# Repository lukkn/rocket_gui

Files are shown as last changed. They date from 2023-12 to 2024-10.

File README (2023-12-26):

# Communication between Teensy and MOTE board

## SETUP INSTRUNCTIONS
1. Connect each MoTE board used to 12V power, connecting to the 2 pins on J1 closest to the top of the board. Upper pin is power, lower pin is ground. Connect each teensy to the router via ethernet, and connect the control console to the same router
2. In the file "Example SD card Root/sensor_min_test.csv", add all necessary sensors and/or actuators, make sure to specify mote number, pin number, and sensor type (see below for sensor types). For ADCs, the pin number is weird. The first digit is the ADC number (counting from the left, starting at 0), and the second digit is the pin number. E.g. ADC pin number 11 is J20, pin 1. For 2ch ADCs, use a pin number of 0 for the left two pins and pin number 1 for the right two pins.
3. Once the teensy is powered and conneted, run gui.py, the orange status light on the teensy will be on if there is a connection. If you need to change any config informaiton, REBOOT THE TEENSY!!

## Sensor Types
* Teensy ADC
* i2c ADC 1ch
* i2c ADC 2ch
* servoPWM
* servoPWM_12V
* Binary GPIO

## Identifying each Teensy and MOTE Board

Each MOTE board will hold a teensy. We can identify each by their unique MOTE number.

They will be last digit of each MOTE's static IP. That digit will be saved as an ascii-value in MoteNumber.txt in SD card.

## Communication Protocol

Protocol used between Teensy and the GUI will be done in **UDP**.

## Types of Functions

There are 4 types of read functions for sensors and 2 types of write functions for actuators.

Each function is assigned an Interface Type Number.

**Read functions:**

1. Teensy ADC
2. i2c ADC 1 channel (ads122c4)
3. i2c ADC 2 channel (ads122c4) (for thermocouple)
4. flowmeter counter

**Write functions:**

5. servo PWM
6. binary gpio

| Operation | Interface Type Number | Sensor/Actuator |
| --- | --- | --- |
| READ | 1 | Teensy ADC |
| READ | 2 | I2C ADC 1 channel (ads122c4) |
| READ | 3 | I2C ADC 2 channel (ads122c4) (for thermocouple) |
| READ | 4 | Flowmeter Counter |
| WRITE | 5 | Servo PWM |
| WRITE | 6 | Binary GPIO |

## Packet Data Structure

Each packet will be sent and received as a **byte array**.

### Sensor Config Commands (Server -> Teensy):

**Byte Array**

| Byte 1  | Byte 2 |
| --- | --- |
| pin_num | config_byte |

**Bit Array of `config_byte`**

| Bit 1 (MSB) | Bit 2 | Bit 3 - 8 |
| --- | --- | --- |
| actuator write command = 0 (since this is not an actuator write command) | actuator state (not used in sensor config packets) | Interface Type Number |

**NB 1.** Byte variable can be of type `char` or `uint8` or `hex` as its eight bits long.

**NB 2.** Given we are dealing with sensors, _Interface Type Number_ is either 1, 2, or 3, and _Bit 1_ and _Bit 2_ are 0.

**NB 3.** Knowing the pin number and sensor type is enough info to call the correct sensor read function, which takes pin number as argument.

### Actuator Write Commands (Server -> Teensy):

**Byte Array**

| Byte 1  | Byte 2 |
| --- | --- |
| pin_num | config_byte |

**Bit Array of `config_byte`**

| Bit 1 (MSB) | Bit 2 | Bit 3 - 8 |
| --- | --- | --- |
| Actuator write command = 1 (because this is an actuator write command) | actuator state | Interface Type Number |

**NB 4.** Given we are dealing with actuators, _Interface Type Number_ is either 4 or 5.

### Sensor Data (Teensy -> Server)

The byte array ar however many sensors there are in each teensy, whose information is provided in config file

Each Teensy will send to the server a differently lengthed byte array.

**Byte Array**

| Byte 1 | Byte 2-5 | Byte 6 | Byte 7-10 | etc. (5 bytes per sensor: 1 pin byte, 4 data bytes) |
| --- | --- | --- | --- | --- |
| pin_num of sensor_1 | data_value of sensor_1 | pin_num of sensor_2 | data_value of sensor_2 | Pin & dava_val of sensors_3-to-n |

**NB 5.** _data_value_ for each sensor is an int (4 bytes).

# To compile Teensy code from command line (without Arduino IDE). NOT USED FOR CURRENT CODE

If cloning this repo to compile firmware, you need to run the following once (to download the teensy4 core):

```
git submodule init
git submodule update
```

To update submodules:

```
git submodule foreach git pull

dependencies:
arm-none-eabi-newlib
arm-none-eabi-gcc
```

The PWMServo library is modified to INVERT the PWM duty cycle because we're using a MOSFET to drive a higher voltage, which inverts the signal
line 198 of PMWServo.cpp

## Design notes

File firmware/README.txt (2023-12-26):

Instructions to build code:

STEP 1
* Open the folder platformio_build in the arduino IDE
* MAKE SURE Teensyduino IS INSTALLED!!!

STEP 2
* Make sure the board selected in the arduino IDE is Teensy 4.1
* If it gives you an error about "sensors_and_servos.h" not found, copy the folder lib/sensors_and_servos into your arduino libraries folder, or make a symlink
	> A symlink is probably better, because if you copy the code into the arudino library and then edit it there, it won't make it into any git commits unless you specifically copy it back
* If you're on Windows, it should be the arudino libraries folder in "Program Files (x86)/Arduino/Libraries"
* If it complains about any other libraries not being installed, install them using the arduino library manager

STEP 3
* Connect the mote board to your computer with an appropriate cable
* Press the "deploy" button in the arduino IDE
* When prompted by Teensyduino, press the button on the mote board
* It should say "done deploying" or something like that
* SEE NEXT STEP **BEFORE** USING MOTE OR POWERING IT WITH A DC POWER SUPPLY

STEP 4
* Make sure the MOTE board is powered either via USB or by a DC Power Supply, NOT BOTH
* If powered via usb, take care to make sure it is only via some kind of hub. Plugging it directly into a computer might damage said computer, do so only at own risk.
* Connect MOTE to a control computer via ethernet, and via USB if you need to read serial outputs (see above note about not combining DC/USB power and about PC saftey with usb)
* Disconnect from BU wifi when communicating with mote via ethernet
* Run the GUI in the Client_GUI folder (see the README file there)
* Make sure the GUI is reading the correct config csv file, and that it is configured correctly.

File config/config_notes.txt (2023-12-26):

Spreadsheet with all components found here:
https://docs.google.com/spreadsheets/d/1thmBCXt51pdb-lDczYVI7NMO4nz0p3LYw5bA1uRQ-AM/edit?usp=sharing

Pin numbers are not shown on this spreadsheet, a pin number of -1 in a config file means the number is unknown.

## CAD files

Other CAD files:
FlaskGUI/python_flask_and_flaskio_and_eventlet_libraries/greenlet/platform/switch_x64_masm.obj
FlaskGUI/python_flask_and_flaskio_and_eventlet_libraries/greenlet/platform/switch_arm64_masm.obj

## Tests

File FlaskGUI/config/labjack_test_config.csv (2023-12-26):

Mote id | Sensor or Actuator | Interface Type | Human Name | Pin | P and ID | unit | min | max
10 | sensor | i2c ADC 2ch | AIN0 | AIN1-AIN0 | AIN0 | Volts | 0 | 5

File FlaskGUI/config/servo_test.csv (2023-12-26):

Mote id | Sensor or Actuator | Interface Type | Human Name | Pin | P and ID
1 | sensor | i2c ADC 1ch | Analog_1 | 42
1 | actuator | servoPWM | Servo_1_5V | 9
1 | actuator | servoPWM | Servo_2_5V | 8
1 | actuator | servoPWM | Servo_3_5V | 7
1 | actuator | servoPWM | Servo_1_7V | 29
1 | actuator | servoPWM | Servo_2_7V | 27
1 | actuator | servoPWM | Servo_3_7V | 25

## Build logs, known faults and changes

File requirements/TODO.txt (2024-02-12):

Functional:
- CRITICAL: ACK/NACK indicator on actuators. Keep current "last sent command" indicator
- Make the ABORT button work. There should be a way to load an abort script from the GUI, 
    and a warning if you try to run a sequence with no abort script loaded
- Forbid arming without a loaded config, and forbid sequences from running disarmed
- Get rid of all the submit buttons, "upload" should inherently submit
- There should be connected indicators
- If a box has sent a packet in the last 1.5s, assume it's there. Otherwise, assume it's disconnected
- Buttons should be greyed out / unclickable when system is disarmed OR disconnected
- Verify autoseq with actuators before autoseq runs
- Arm/Disarm button spamming while app.py is not running will lead to all commands being received on restart ;; check this for actuator presses as well, we default to disarm so fixing the first issue should fix the second but not a good aproach

Stylistic:
- Make it look nice!
- Make the sensor graphs a 2xN grid

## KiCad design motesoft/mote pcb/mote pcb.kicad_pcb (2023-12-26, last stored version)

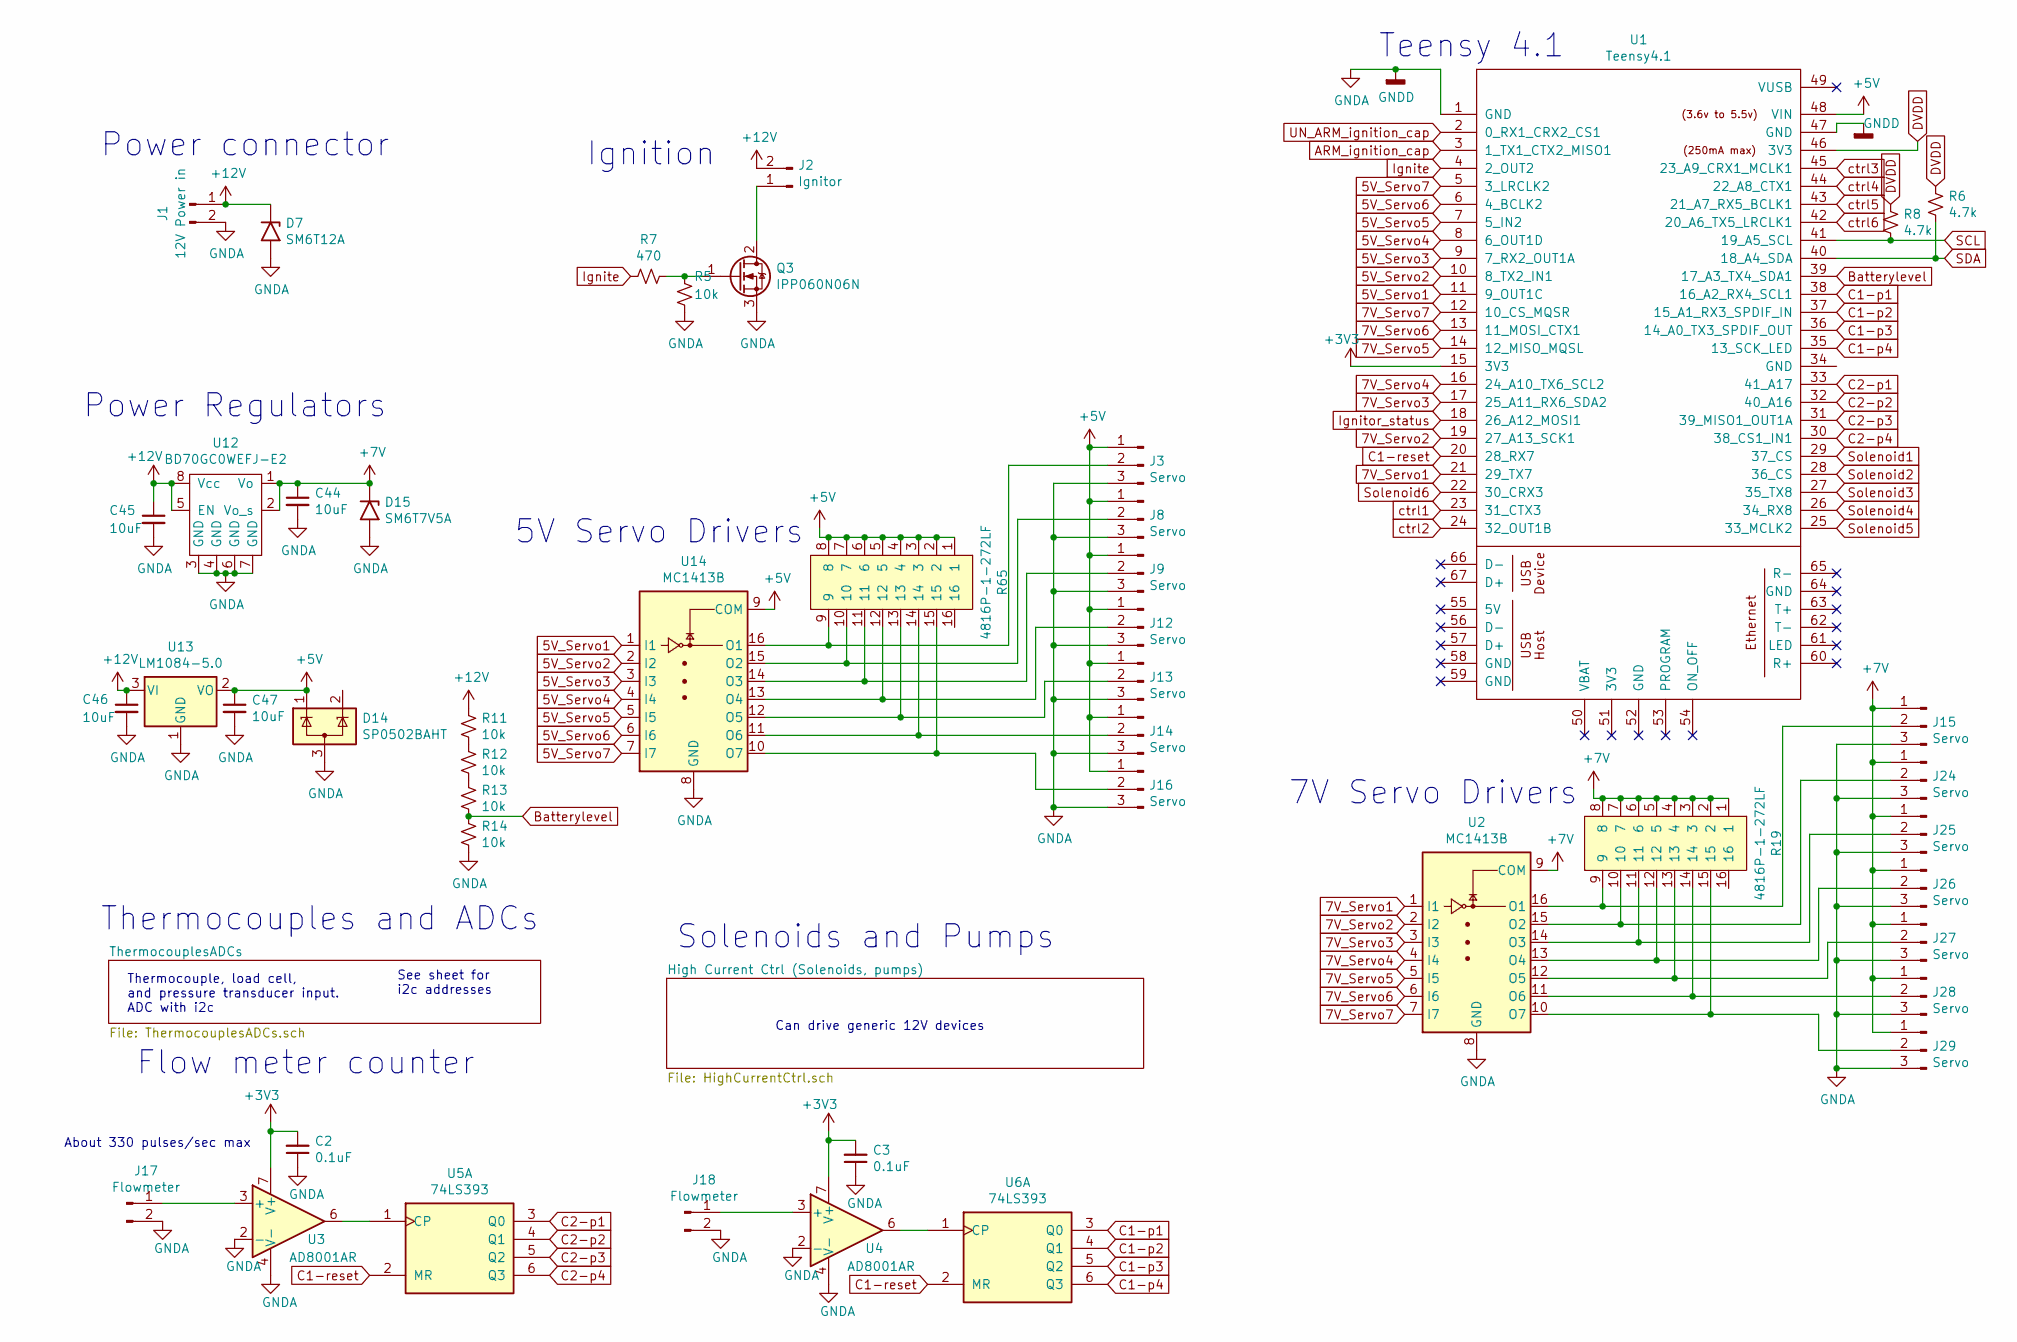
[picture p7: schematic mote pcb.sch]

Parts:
C2, C3: 0.1uF; C_0603_1608Metric_Pad1.08x0.95mm_HandSolder; LCSC Part # C14663
C44, C45, C46, C47: 10uF; C_0603_1608Metric_Pad1.08x0.95mm_HandSolder; LCSC Part # C19702
D7: SM6T12A; D_SMB
D14: SP0502BAHT; SOT-23
D15: SM6T7V5A; D_SMB
J1: 12V Power in; JST_EH_B4B-EH-A_1x04_P2.50mm_Vertical
J2: Ignitor; JST_EH_B4B-EH-A_1x04_P2.50mm_Vertical
J3, J8, J9, J12, J13, J14, J15, J16, J24, J25, J26, J27, J28, J29: Servo; JST_EH_B4B-EH-A_1x04_P2.50mm_Vertical
J17, J18: Flowmeter; JST_EH_B4B-EH-A_1x04_P2.50mm_Vertical
Q3: IPP060N06N; TO-220-3_Vertical
R5, R11, R12, R13, R14: 10k; R_0603_1608Metric_Pad0.98x0.95mm_HandSolder; LCSC Part # C25804
R6, R8: 4.7k; R_0603_1608Metric_Pad0.98x0.95mm_HandSolder; LCSC Part # C23162
R7: 470; R_0603_1608Metric_Pad0.98x0.95mm_HandSolder; LCSC Part # C23179
R19, R65: 4816P-1-272LF; SOIC-16W_5.3x10.2mm_P1.27mm
U1: Teensy4.1; Teensy41
U2, U14: MC1413B; SOIC-16_3.9x9.9mm_P1.27mm
U3, U4: AD8001AR; SOIC-8_3.9x4.9mm_P1.27mm
U5, U6: 74LS393; SOIC-14_3.9x8.7mm_P1.27mm
U12: BD70GC0WEFJ-E2; SOIC-8-1EP_3.9x4.9mm_P1.27mm_EP2.29x3mm_ThermalVias
U13: LM1084-5.0; TO-263-3_TabPin2

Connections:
5V_Servo1: U1.11 (9_OUT1C), U14.1 (I1)
5V_Servo2: U1.10 (8_TX2_IN1), U14.2 (I2)
5V_Servo3: U1.9 (7_RX2_OUT1A), U14.3 (I3)
5V_Servo4: U1.8 (6_OUT1D), U14.4 (I4)
5V_Servo5: U1.7 (5_IN2), U14.5 (I5)
5V_Servo6: U1.6 (4_BCLK2), U14.6 (I6)
5V_Servo7: U1.5 (3_LRCLK2), U14.7 (I7)
7V_Servo1: U1.21 (29_TX7), U2.1 (I1)
7V_Servo2: U1.19 (27_A13_SCK1), U2.2 (I2)
7V_Servo3: U1.17 (25_A11_RX6_SDA2), U2.3 (I3)
7V_Servo4: U1.16 (24_A10_TX6_SCL2), U2.4 (I4)
7V_Servo5: U1.14 (12_MISO_MQSL), U2.5 (I5)
7V_Servo6: U1.13 (11_MOSI_CTX1), U2.6 (I6)
7V_Servo7: U1.12 (10_CS_MQSR), U2.7 (I7)
+3V3: C2.2, C3.2, U1.15 (3V3), U3.7 (V+), U4.7 (V+); also elsewhere on the board
+5V: C47.1, D14.1 (K), J3.1, J8.1, J9.1, J12.1, J13.1, J14.1, J16.1, R65.1, R65.2, R65.3, R65.4, R65.5, R65.6, R65.7, R65.8, U1.48 (VIN), U13.2 (VO), U14.9 (COM)
+7.5V: C44.1, D15.1 (A1), J15.1, J24.1, J25.1, J26.1, J27.1, J28.1, J29.1, R19.1, R19.2, R19.3, R19.4, R19.5, R19.6, R19.7, R19.8, U2.9 (COM), U12.1 (Vo), U12.2 (Vo_s)
+12V: C45.1, C46.1, D7.1 (A1), J1.1, J2.2, R11.1, U12.5 (EN), U12.8 (Vcc), U13.3 (VI); also elsewhere on the board
Batterylevel: R13.2, R14.1, U1.39 (17_A3_TX4_SDA1)
C1-p1: U1.38 (16_A2_RX4_SCL1), U6.3 (Q0)
C1-p2: U1.37 (15_A1_RX3_SPDIF_IN), U6.4 (Q1)
C1-p3: U1.36 (14_A0_TX3_SPDIF_OUT), U6.5 (Q2)
C1-p4: U1.35 (13_SCK_LED), U6.6 (Q3)
C1-reset: U1.20 (28_RX7), U5.2 (MR), U6.2 (MR)
C2-p1: U1.33 (41_A17), U5.3 (Q0)
C2-p2: U1.32 (40_A16), U5.4 (Q1)
C2-p3: U1.31 (39_MISO1_OUT1A), U5.5 (Q2)
C2-p4: U1.30 (38_CS1_IN1), U5.6 (Q3)
DVDD: R6.1, R8.1, U1.46 (3V3)
GNDA: C2.1, C3.1, C44.2, C45.2, C46.2, C47.2, D7.2 (A2), D14.3 (A), D15.2 (A2), J1.2, J3.3, J8.3, J9.3, J12.3, J13.3, J14.3, J15.3, J16.3, J17.2, J18.2, J24.3, J25.3, J26.3, J27.3, J28.3, J29.3, Q3.3 (S), R5.2, R14.2, U1.1 (GND), U1.47 (GND), U2.8 (GND), U3.2 (-), U3.4 (V-), U4.2 (-), U4.4 (V-), U12.3 (GND), U12.4 (GND), U12.6 (GND), U12.7 (GND), U13.1 (GND), U14.8 (GND); also elsewhere on the board
Ignite: R7.2, U1.4 (2_OUT2)
unnamed: J2.1, Q3.2 (D)
unnamed: J3.2, R65.9, U14.16 (O1)
unnamed: J8.2, R65.10, U14.15 (O2)
unnamed: J9.2, R65.11, U14.14 (O3)
unnamed: J12.2, R65.12, U14.13 (O4)
unnamed: J13.2, R65.13, U14.12 (O5)
unnamed: J14.2, R65.14, U14.11 (O6)
unnamed: J15.2, R19.9, U2.16 (O1)
unnamed: J16.2, R65.15, U14.10 (O7)
unnamed: J17.1, U3.3 (+)
unnamed: J18.1, U4.3 (+)
unnamed: J24.2, R19.10, U2.15 (O2)
unnamed: J25.2, R19.11, U2.14 (O3)
unnamed: J26.2, R19.12, U2.13 (O4)
unnamed: J27.2, R19.13, U2.12 (O5)
unnamed: J28.2, R19.14, U2.11 (O6)
unnamed: J29.2, R19.15, U2.10 (O7)
unnamed: Q3.1 (G), R5.1, R7.1
unnamed: R11.2, R12.1
unnamed: R12.2, R13.1
unnamed: U3.6, U5.1 (CP)
unnamed: U4.6, U6.1 (CP)
SCL: R8.2, U1.41 (19_A5_SCL); also elsewhere on the board
SDA: R6.2, U1.40 (18_A4_SDA); also elsewhere on the board
Solenoid1: U1.29 (37_CS); also elsewhere on the board
Solenoid2: U1.28 (36_CS); also elsewhere on the board
Solenoid3: U1.27 (35_TX8); also elsewhere on the board
Solenoid4: U1.26 (34_RX8); also elsewhere on the board
Solenoid5: U1.25 (33_MCLK2); also elsewhere on the board
Solenoid6: U1.22 (30_CRX3); also elsewhere on the board
ctrl1: U1.23 (31_CTX3); also elsewhere on the board
ctrl2: U1.24 (32_OUT1B); also elsewhere on the board
ctrl3: U1.45 (23_A9_CRX1_MCLK1); also elsewhere on the board
ctrl4: U1.44 (22_A8_CTX1); also elsewhere on the board
ctrl5: U1.43 (21_A7_RX5_BCLK1); also elsewhere on the board
ctrl6: U1.42 (20_A6_TX5_LRCLK1); also elsewhere on the board

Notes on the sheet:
Thermocouple, load cell, and pressure transducer input. ADC with i2c
See sheet for i2c addresses
Ignition
Thermocouples and ADCs
Flow meter counter
Teensy 4.1
About 330 pulses/sec max
Power connector
7V Servo Drivers
Can drive generic 12V devices
Solenoids and Pumps
5V Servo Drivers
Power Regulators

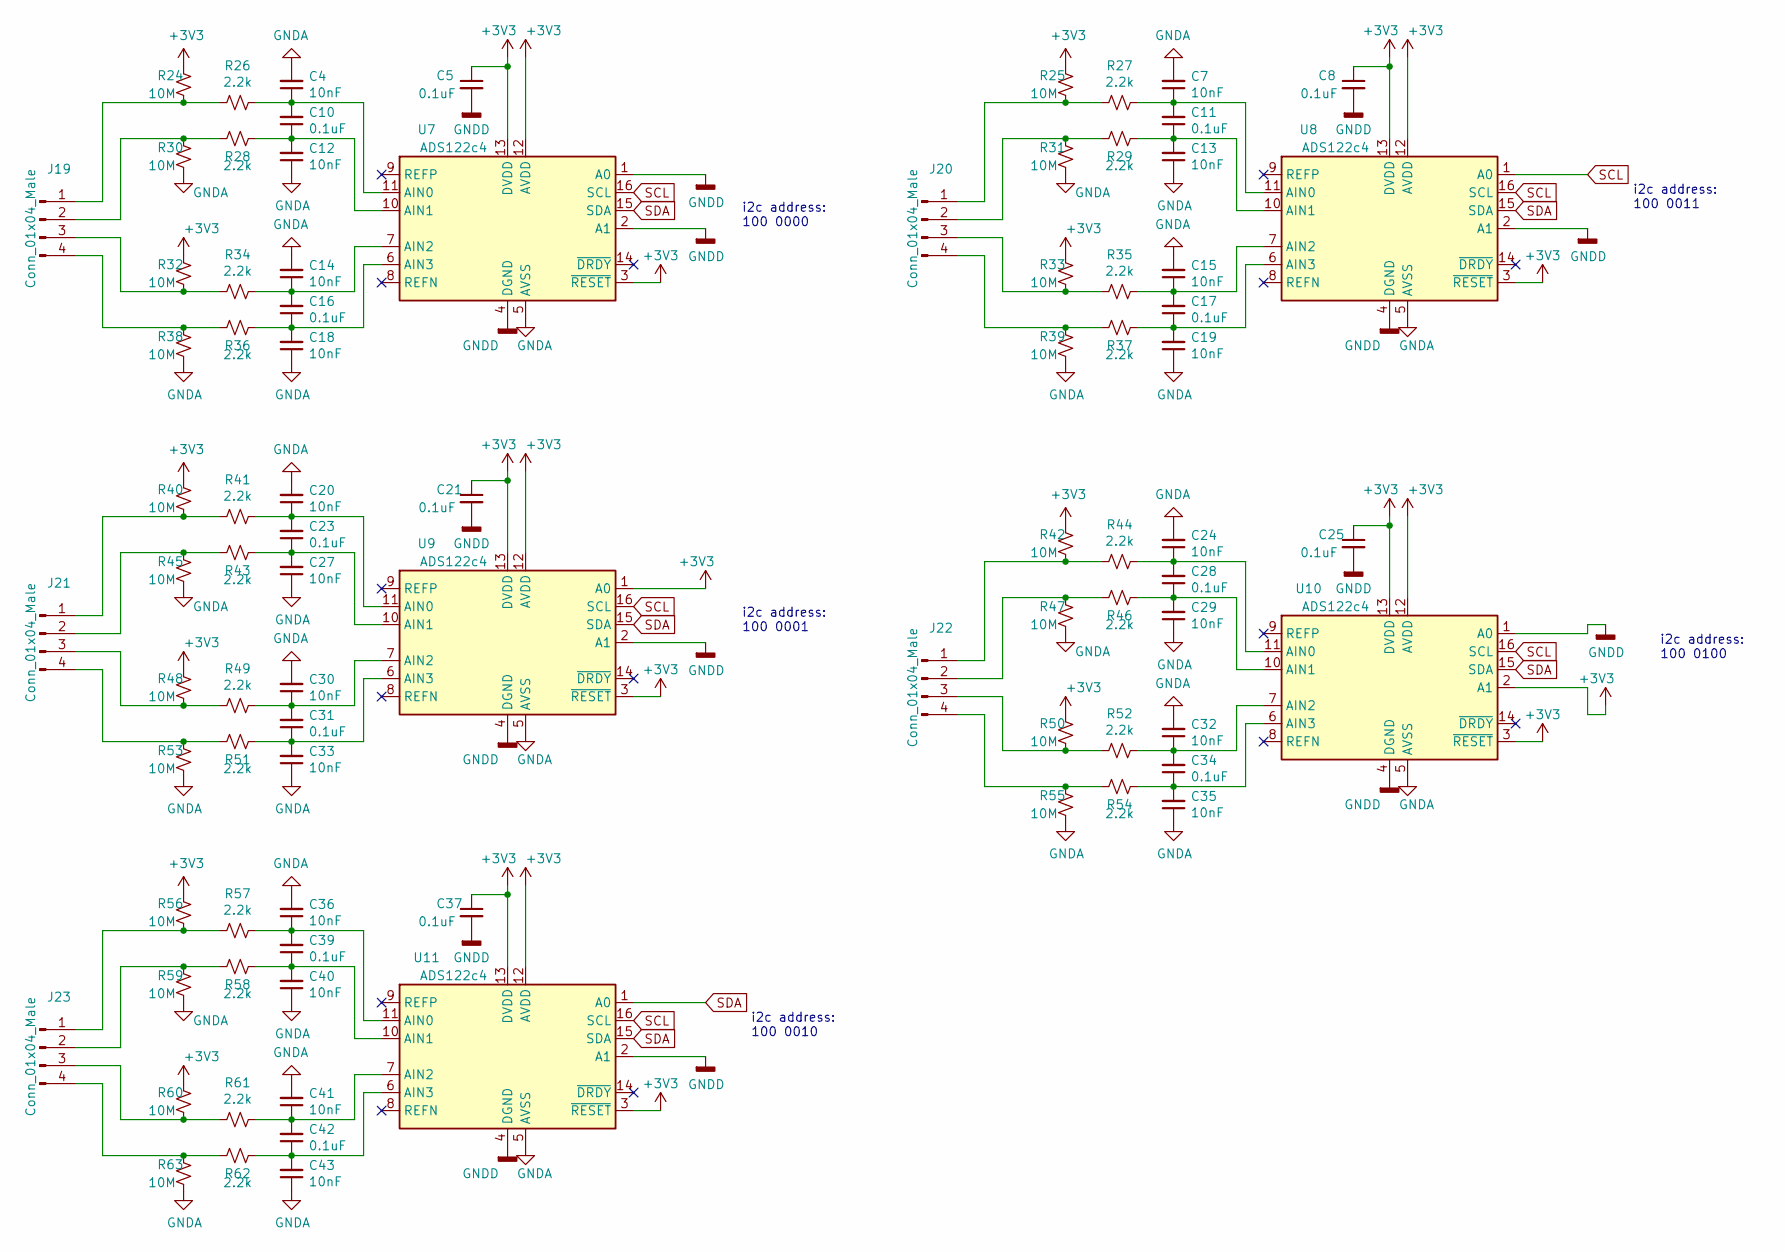
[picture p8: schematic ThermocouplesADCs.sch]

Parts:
C4, C7, C12, C13, C14, C15, C18, C19, C20, C24, C27, C29, C30, C32, C33, C35, C36, C40, C41, C43: 10nF; C_0603_1608Metric_Pad1.08x0.95mm_HandSolder; LCSC Part # C57112
C5, C8, C10, C11, C16, C17, C21, C23, C25, C28, C31, C34, C37, C39, C42: 0.1uF; C_0603_1608Metric_Pad1.08x0.95mm_HandSolder; LCSC Part # C14663
J19, J20, J21, J22, J23: Conn_01x04_Male; JST_EH_B4B-EH-A_1x04_P2.50mm_Vertical
R24, R25, R30, R31, R32, R33, R38, R39, R40, R42, R45, R47, R48, R50, R53, R55, R56, R59, R60, R63: 10M; R_0603_1608Metric_Pad0.98x0.95mm_HandSolder; LCSC Part # C7250
R26, R27, R28, R29, R34, R35, R36, R37, R41, R43, R44, R46, R49, R51, R52, R54, R57, R58, R61, R62: 2.2k; R_0603_1608Metric_Pad0.98x0.95mm_HandSolder; LCSC Part # C4190
U7, U8, U9, U10, U11: ADS122c4; TSSOP-16_4.4x5mm_P0.65mm

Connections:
+3V3: C5.1, C8.1, C21.1, C25.1, C37.1, R24.2, R25.2, R32.2, R33.2, R40.2, R42.2, R48.2, R50.2, R56.2, R60.2, U7.3 (~RESET), U7.12 (AVDD), U7.13 (DVDD), U8.3 (~RESET), U8.12 (AVDD), U8.13 (DVDD), U9.1 (A0), U9.3 (~RESET), U9.12 (AVDD), U9.13 (DVDD), U10.2 (A1), U10.3 (~RESET), U10.12 (AVDD), U10.13 (DVDD), U11.3 (~RESET), U11.12 (AVDD), U11.13 (DVDD); also elsewhere on the board
GNDA: C4.2, C5.2, C7.2, C8.2, C12.1, C13.1, C14.2, C15.2, C18.1, C19.1, C20.2, C21.2, C24.2, C25.2, C27.1, C29.1, C30.2, C32.2, C33.1, C35.1, C36.2, C37.2, C40.1, C41.2, C43.1, R30.1, R31.1, R38.1, R39.1, R45.1, R47.1, R53.1, R55.1, R59.1, R63.1, U7.1 (A0), U7.2 (A1), U7.4 (DGND), U7.5 (AVSS), U8.2 (A1), U8.4 (DGND), U8.5 (AVSS), U9.2 (A1), U9.4 (DGND), U9.5 (AVSS), U10.1 (A0), U10.4 (DGND), U10.5 (AVSS), U11.2 (A1), U11.4 (DGND), U11.5 (AVSS); also elsewhere on the board
unnamed: C10.1, C12.2, R28.2, U7.10 (AIN1)
unnamed: C4.1, C10.2, R26.2, U7.11 (AIN0)
unnamed: C11.1, C13.2, R29.2, U8.10 (AIN1)
unnamed: C7.1, C11.2, R27.2, U8.11 (AIN0)
unnamed: C14.1, C16.2, R34.2, U7.7 (AIN2)
unnamed: C15.1, C17.2, R35.2, U8.7 (AIN2)
unnamed: C16.1, C18.2, R36.2, U7.6 (AIN3)
unnamed: C17.1, C19.2, R37.2, U8.6 (AIN3)
unnamed: C20.1, C23.2, R41.2, U9.11 (AIN0)
unnamed: C23.1, C27.2, R43.2, U9.10 (AIN1)
unnamed: C24.1, C28.2, R44.2, U10.11 (AIN0)
unnamed: C28.1, C29.2, R46.2, U10.10 (AIN1)
unnamed: C30.1, C31.2, R49.2, U9.7 (AIN2)
unnamed: C31.1, C33.2, R51.2, U9.6 (AIN3)
unnamed: C32.1, C34.2, R52.2, U10.7 (AIN2)
unnamed: C34.1, C35.2, R54.2, U10.6 (AIN3)
unnamed: C36.1, C39.2, R57.2, U11.11 (AIN0)
unnamed: C39.1, C40.2, R58.2, U11.10 (AIN1)
unnamed: C41.1, C42.2, R61.2, U11.7 (AIN2)
unnamed: C42.1, C43.2, R62.2, U11.6 (AIN3)
unnamed: J19.1, R24.1, R26.1
unnamed: J19.2, R28.1, R30.2
unnamed: J19.3, R32.1, R34.1
unnamed: J19.4, R36.1, R38.2
unnamed: J20.1, R25.1, R27.1
unnamed: J20.2, R29.1, R31.2
unnamed: J20.3, R33.1, R35.1
unnamed: J20.4, R37.1, R39.2
unnamed: J21.1, R40.1, R41.1
unnamed: J21.2, R43.1, R45.2
unnamed: J21.3, R48.1, R49.1
unnamed: J21.4, R51.1, R53.2
unnamed: J22.1, R42.1, R44.1
unnamed: J22.2, R46.1, R47.2
unnamed: J22.3, R50.1, R52.1
unnamed: J22.4, R54.1, R55.2
unnamed: J23.1, R56.1, R57.1
unnamed: J23.2, R58.1, R59.2
unnamed: J23.3, R60.1, R61.1
unnamed: J23.4, R62.1, R63.2
SCL: U7.16 (SCL), U8.1 (A0), U8.16 (SCL), U9.16 (SCL), U10.16 (SCL), U11.16 (SCL); also elsewhere on the board
SDA: U7.15 (SDA), U8.15 (SDA), U9.15 (SDA), U10.15 (SDA), U11.1 (A0), U11.15 (SDA); also elsewhere on the board

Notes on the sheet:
i2c address: 100 0000
i2c address: 100 0001
i2c address: 100 0010
i2c address: 100 0011
i2c address: 100 0100

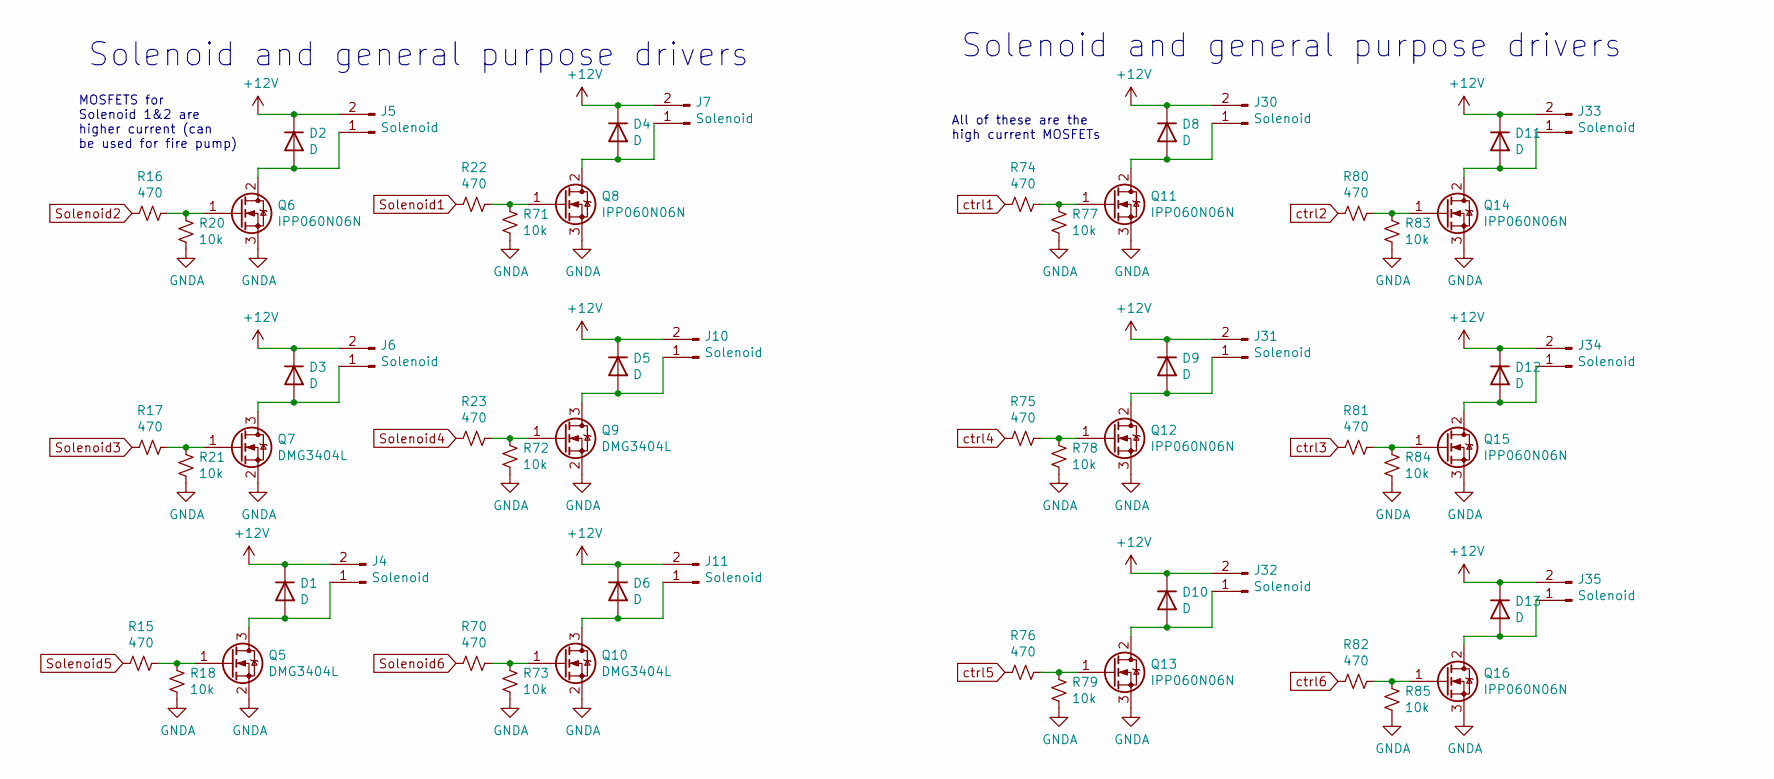
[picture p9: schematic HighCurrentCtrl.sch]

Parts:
D1, D2, D3, D4, D5, D6, D8, D9, D10, D11, D12, D13: D; D_SOD-123; LCSC Part # C8598
J4, J5, J6, J7, J10, J11, J30, J31, J32, J33, J34, J35: Solenoid; JST_EH_B4B-EH-A_1x04_P2.50mm_Vertical
Q5, Q7, Q9, Q10: DMG3404L; SOT-23
Q6, Q8, Q11, Q12, Q13, Q14, Q15, Q16: IPP060N06N; TO-220-3_Vertical
R15, R16, R17, R22, R23, R70, R74, R75, R76, R80, R81, R82: 470; R_0603_1608Metric_Pad0.98x0.95mm_HandSolder; LCSC Part # C23179
R18, R20, R21, R71, R72, R73, R77, R78, R79, R83, R84, R85: 10k; R_0603_1608Metric_Pad0.98x0.95mm_HandSolder; LCSC Part # C25804

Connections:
+12V: D1.1 (K), D2.1 (K), D3.1 (K), D4.1 (K), D5.1 (K), D6.1 (K), D8.1 (K), D9.1 (K), D10.1 (K), D11.1 (K), D12.1 (K), D13.1 (K), J4.2, J5.2, J6.2, J7.2, J10.2, J11.2, J30.2, J31.2, J32.2, J33.2, J34.2, J35.2; also elsewhere on the board
GNDA: Q5.2 (S), Q6.3 (S), Q7.2 (S), Q8.3 (S), Q9.2 (S), Q10.2 (S), Q11.3 (S), Q12.3 (S), Q13.3 (S), Q14.3 (S), Q15.3 (S), Q16.3 (S), R18.2, R20.2, R21.2, R71.2, R72.2, R73.2, R77.2, R78.2, R79.2, R83.2, R84.2, R85.2; also elsewhere on the board
unnamed: D1.2 (A), J4.1, Q5.3 (D)
unnamed: D2.2 (A), J5.1, Q6.2 (D)
unnamed: D3.2 (A), J6.1, Q7.3 (D)
unnamed: D4.2 (A), J7.1, Q8.2 (D)
unnamed: D5.2 (A), J10.1, Q9.3 (D)
unnamed: D6.2 (A), J11.1, Q10.3 (D)
unnamed: D8.2 (A), J30.1, Q11.2 (D)
unnamed: D9.2 (A), J31.1, Q12.2 (D)
unnamed: D10.2 (A), J32.1, Q13.2 (D)
unnamed: D11.2 (A), J33.1, Q14.2 (D)
unnamed: D12.2 (A), J34.1, Q15.2 (D)
unnamed: D13.2 (A), J35.1, Q16.2 (D)
unnamed: Q5.1 (G), R15.1, R18.1
unnamed: Q6.1 (G), R16.1, R20.1
unnamed: Q7.1 (G), R17.1, R21.1
unnamed: Q8.1 (G), R22.1, R71.1
unnamed: Q9.1 (G), R23.1, R72.1
unnamed: Q10.1 (G), R70.1, R73.1
unnamed: Q11.1 (G), R74.1, R77.1
unnamed: Q12.1 (G), R75.1, R78.1
unnamed: Q13.1 (G), R76.1, R79.1
unnamed: Q14.1 (G), R80.1, R83.1
unnamed: Q15.1 (G), R81.1, R84.1
unnamed: Q16.1 (G), R82.1, R85.1
Solenoid1: R22.2; also elsewhere on the board
Solenoid2: R16.2; also elsewhere on the board
Solenoid3: R17.2; also elsewhere on the board
Solenoid4: R23.2; also elsewhere on the board
Solenoid5: R15.2; also elsewhere on the board
Solenoid6: R70.2; also elsewhere on the board
ctrl1: R74.2; also elsewhere on the board
ctrl2: R80.2; also elsewhere on the board
ctrl3: R81.2; also elsewhere on the board
ctrl4: R75.2; also elsewhere on the board
ctrl5: R76.2; also elsewhere on the board
ctrl6: R82.2; also elsewhere on the board

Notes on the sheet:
MOSFETS for Solenoid 1&2 are higher current (can be used for fire pump)
Solenoid and general purpose drivers
All of these are the high current MOSFETs

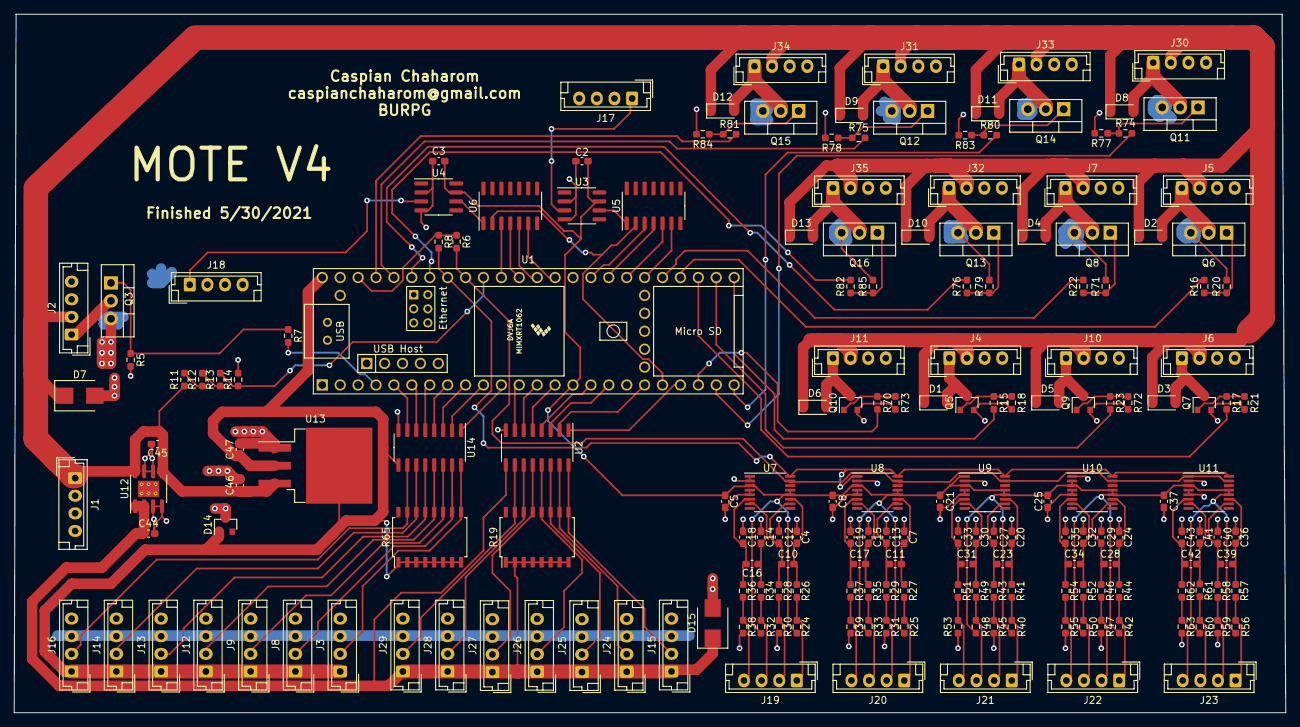
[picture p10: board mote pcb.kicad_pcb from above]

Board: 2 copper layers, 180.3 x 99.1 mm, 192 parts (0 on the bottom side), 131 nets.

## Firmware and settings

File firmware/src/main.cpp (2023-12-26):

#include <vector>
#include <Arduino.h>
#include <SPI.h>
#include <SD.h>
#include <NativeEthernet.h>    // Must use NativeEthernet libraries with Teensy
#include <NativeEthernetUdp.h> // Must use NativeEthernet libraries with Teensy
#include <PWMServo.h>
#include <sensors_and_servos.h>
#include <SparkFun_ADS122C04_ADC_Arduino_Library.h>
#include <Wire.h>

#include "consts.h"
#include "settings.h"

byte* mac;

unsigned int localPort = PORT; // Local port to listen on

// Buffers for receiving and sending data
char packetBuffer[64];
//char replyBuffer[] = "acknowledged";

// Bool to indicate recieve or transmit data
// TRUE for Rx - FALSE for Tx
// bool RxTx = true;

SFE_ADS122C04* temp;

AD7193_arg_t spi_adc_config_1;
AD7193_arg_t spi_adc_config_2;

struct SingleSensorConfig {
  uint8_t pin_num;
  uint8_t interface_type_number;
  SFE_ADS122C04* adc_ptr;
};

std::vector<SingleSensorConfig> all_sensors;
std::vector<char> telemetry_to_send;

// Variables for saving received data
bool actuator_write_command;
bool actuator_state;
uint8_t interface_type_number;
uint8_t pin_num;

char moteID;
char *deviceType;
char *interface;
char *humanName;
unsigned int pin;
void parsePacket(char *input);

// An EthernetUDP instance to let us send and receive packets over UDP
EthernetUDP Udp;

// set up variables using the SD utility library functions:
Sd2Card card;
SdVolume volume;
SdFile root;

// Teensy 3.5 & 3.6 & 4.1 on-board: BUILTIN_SDCARD
const int chipSelect = BUILTIN_SDCARD;

//which solenoids to set OPEN/CLOSE on startup
//These are the pins mapped to CTRL 1-6 and SOLENOID 1-6 on the schematic
int solenoid_pins[] = {};
int inverse_solenoid_pins_mote1[] = MOTE1_INITIALLY_POWERED_SOLENOIDS;
int inverse_solenoid_pins_mote2[] = MOTE2_INITIALLY_POWERED_SOLENOIDS;
int inverse_solenoid_pins_mote3[] = MOTE3_INITIALLY_POWERED_SOLENOIDS;

int loop_delay_ms = 1;
uint64_t ticks = 0;

bool do_fireX = DO_FIREX;
bool hot_fireX = false;

//IN MILLISECONDS. IF YOU SET IT IN SECONDS, MINUTES, HOURS, ETC, YOU WILL HAVE A BAD TIME!
unsigned long cold_fireX_time;
unsigned long cold_fireX_delay = COLD_FIREX_TIME_DEFAULT; //fake number
unsigned long hot_fireX_time;
unsigned long hot_fireX_delay = HOT_FIREX_TIME_DEFAULT;

//bang-bang control bools
bool do_bang_bang_ox = false;
bool do_bang_bang_fuel = false;

//TODO make this read from a file instead of hardcoded
//Bang-Bang config data
bool VENT_OX_flag = false;
bool PRESS_OX_flag = false;
bool VENT_FUEL_flag = false;
bool PRESS_FUEL_flag = false;

//bullshit pin nums, replace with real ones or config file system
int PRESS_OX_pin_nums[] = NO2_PRESS_PIN_NUM; //MOSFET J34
int VENT_OX_pin_nums[] = NO2_VENT_PIN_NUM; //MOSFET J33
int PRESS_FUEL_pin_nums[] = IPA_PRESS_PIN_NUM; //MOSFET J30
int VENT_FUEL_pin_nums[] = IPA_VENT_PIN_NUM; //MOSFET J7

int sensor_ox_pin_num = NO2_SENSOR_PIN_NUM;
SFE_ADS122C04* ox_adc_ptr;
int sensor_fuel_pin_num = IPA_SENSOR_PIN_NUM;
SFE_ADS122C04* fuel_adc_ptr;

void write_to_telemetry_array(std::vector<char>& telemetry_to_send, int sensor_reading, int i, int pin_num)
{
  //Serial.println("Starting write_to_telemetry_array");
  //telemetry_to_send.resize(telemetry_to_send.size()+5);
	uint8_t byte1 =  sensor_reading & 0x000000ff;
	uint8_t byte2 = (sensor_reading & 0x0000ff00) >> 8;
	uint8_t byte3 = (sensor_reading & 0x00ff0000) >> 16;
	uint8_t byte4 = (sensor_reading & 0xff000000) >> 24;
	telemetry_to_send.push_back((uint8_t)pin_num);
	telemetry_to_send.push_back(byte1);
	telemetry_to_send.push_back(byte2);
	telemetry_to_send.push_back(byte3);
	telemetry_to_send.push_back(byte4);
}

void hot_fail(){
  if (moteID == '3'){
    digital_write(FIREX_PIN_NUM, false);

    for (int n : VENT_FUEL_pin_nums){
      digital_write(n, false);
    }

    for (int n : VENT_OX_pin_nums){
      digital_write(n, false);
    }
  }

    if (moteID == '1')
      for (int pin : inverse_solenoid_pins_mote1){
          digital_write(pin, false);
      }
    if (moteID == '2')
      for (int pin : inverse_solenoid_pins_mote2){
          digital_write(pin, false);
      }
    if (moteID == '3')
      for (int pin : inverse_solenoid_pins_mote2){
          digital_write(pin, false);
      }
}

void cold_fail(){
  digital_write(FIREX_PIN_NUM, false);
}

void parsePacket(char *data)
{
    pin_num = data[0];
    uint8_t config_byte = data[1];
    actuator_write_command = (config_byte & 0b10000000) == 0b10000000;
    actuator_state = (config_byte & 0b01000000) == 0b01000000;
    interface_type_number = (config_byte & 0b00111111);
  
    if (actuator_write_command)
    {
      #ifdef ENABLE_DEBUG
        Serial.print("Setting pin ");
        Serial.print(pin_num);
        Serial.print(" to ");
        Serial.print(actuator_state);
        Serial.println(" with interface ");
      #endif
      if (interface_type_number == PWM_SERVO)
      {
          int servo_angle = 0;
          if (actuator_state){
            servo_angle = 180;
          } else {
            servo_angle = 0;
          }
          #ifdef ENABLE_DEBUG
            Serial.println("servoPWM");
            Serial.print("Pin num: ");
            Serial.println(pin_num);
            Serial.print("State: ");
            Serial.println(servo_angle);
          #endif
          //TODO: set servo pin_num to actuator_state
          servo_write(PWMServo(), pin_num, servo_angle);
      }
      else if (interface_type_number == BINARY_LOAD_SWITCH){
          //pinMode(pin_num, OUTPUT);
          //digitalWrite(pin_num, LOW);
          digital_write(pin_num, actuator_state);
      } 
      else if (interface_type_number == BANG_BANG_CONTROL){
        #ifdef ENABLE_DEBUG
        Serial.println("toggle bang-bang");
        Serial.println(pin_num);
        Serial.println(actuator_state);
        #endif
  
        if(pin_num == 1){
          do_bang_bang_ox = actuator_state;
          if (!do_bang_bang_ox){
            Serial.println("Shutting all bang-bang valves.");
            for (int n : VENT_OX_pin_nums){
              digital_write(n, false);
            }
            for (int n : PRESS_OX_pin_nums){
              digital_write(n, false);
            }
          }
        }
        if(pin_num == 0){
          do_bang_bang_fuel = actuator_state;
          if (!do_bang_bang_fuel){
            Serial.println("Shutting all bang-bang valves.");
            for (int n : VENT_FUEL_pin_nums){
              digital_write(n, false);
            }
            for (int n : PRESS_FUEL_pin_nums){
              digital_write(n, false);
            }
          }
        }
      }
      else if (interface_type_number == AUTO_FIREX_CONTROL){
        hot_fireX = actuator_state;
        Serial.print("Set HOT_FIREX to: ");
        Serial.println(hot_fireX);
      }
      else if (interface_type_number == HEARTBEAT){
        Serial.println("Heartbeat recieved");
      }
      else
      {
        Serial.println(interface_type_number);
        Serial.println("Error. Actuator Interface number is not valid");
      }
      //ACK HERE
      if(interface_type_number != HEARTBEAT && interface_type_number != AUTO_FIREX_CONTROL && interface_type_number != BANG_BANG_CONTROL) 
        write_to_telemetry_array(telemetry_to_send, (int)actuator_state, 0, pin_num + 100);
      //End ACK
    }else{  // if a sensor config command, save the sensor config
      Serial.println("Recieved a sensor config command");
    	SingleSensorConfig new_sensor;
    	new_sensor.pin_num = pin_num;
    	new_sensor.interface_type_number = interface_type_number; 
    	
    	if(new_sensor.interface_type_number == TEENSY_ADC){ 
        // Interal Teensy ADC. No-op.
    	}else if(new_sensor.interface_type_number == I2C_ADC_1CH || new_sensor.interface_type_number == I2C_ADC_2CH || new_sensor.interface_type_number == INTERNAL_TEMP ||
    	        (new_sensor.interface_type_number >= I2C_ADC_2CH_MIN_GAIN && new_sensor.interface_type_number <= I2C_ADC_2CH_MAX_GAIN)){ // i2c ADC
        new_sensor.adc_ptr = new SFE_ADS122C04;
        new_sensor.adc_ptr->begin((new_sensor.pin_num/10 + 64), Wire);

        new_sensor.adc_ptr->setDataRate(ADS122C04_DATA_RATE_1000SPS);
        //TURBO MODE
        //HELL YEAH
        new_sensor.adc_ptr->setOperatingMode(ADS122C04_OP_MODE_TURBO);

        
        Serial.println("Began ADC!");
    	}else if(new_sensor.interface_type_number == FLOWMETER){ // FlowMeter
    		//TODO configure flowmeter (using new_sensor.pin_num)
      }
      else if (new_sensor.interface_type_number == SPI_ADC_1CH) {
        if (new_sensor.pin_num / 10 == 0) {
          spi_adc_config_1.channel_bits |= (1 << (new_sensor.pin_num % 10)) << 8;
          spi_adc_config_1.differential = false;
          spi_adc_config_1.internal_temp = false;
          spi_adc_config_1.pga_gain = 1;
          spi_adc_config_1.spi_num = 0;
          configure_AD7193(spi_adc_config_1);
        } else {
          spi_adc_config_2.channel_bits |= (1 << (new_sensor.pin_num % 10)) << 8;
          spi_adc_config_2.differential = false;
          spi_adc_config_2.internal_temp = false;
          spi_adc_config_2.pga_gain = 1;
          spi_adc_config_2.spi_num = 1;
          configure_AD7193(spi_adc_config_2);
        }
      } else if (new_sensor.interface_type_number >= SPI_ADC_2CH && new_sensor.interface_type_number <= SPI_ADC_2CH_MAX_GAIN) {
        if (new_sensor.pin_num / 10 == 0) {
          spi_adc_config_1.channel_bits |= (1 << (new_sensor.pin_num % 10)) << 8;
          spi_adc_config_1.differential = true;
          spi_adc_config_1.internal_temp = false;
          spi_adc_config_1.pga_gain = (int)pow(2, new_sensor.interface_type_number - SPI_ADC_2CH);
          spi_adc_config_1.spi_num = 0;
          configure_AD7193(spi_adc_config_1);
        } else {
          spi_adc_config_2.channel_bits |= (1 << (new_sensor.pin_num % 10)) << 8;
          spi_adc_config_2.differential = true;
          spi_adc_config_2.internal_temp = false;
          spi_adc_config_2.pga_gain = (int)pow(2, new_sensor.interface_type_number - SPI_ADC_2CH);
          spi_adc_config_2.spi_num = 1;
          configure_AD7193(spi_adc_config_2);
        }
      } else if (new_sensor.interface_type_number == INTERNAL_TEMP) {
        if (new_sensor.pin_num / 10 == 0) {
          spi_adc_config_1.channel_bits = (1 << 0b1000) << 8;
          spi_adc_config_1.differential = false;
          spi_adc_config_1.internal_temp = true;
          spi_adc_config_1.pga_gain = 1;
          spi_adc_config_1.spi_num = 0;
          configure_AD7193(spi_adc_config_1);
        } else {
          spi_adc_config_2.channel_bits = (1 << 0b1000) << 8;
          spi_adc_config_2.differential = false;
          spi_adc_config_2.internal_temp = true;
          spi_adc_config_2.pga_gain = 1;
          spi_adc_config_2.spi_num = 1;
          configure_AD7193(spi_adc_config_2);
        }
      }
      else if (new_sensor.interface_type_number == SENSOR_CLEAR_CODE) {
        all_sensors.clear();
        return;
    	}else{
	    	Serial.println("Error. Interface number is not valid");
    	}
      
      
      all_sensors.push_back(new_sensor);
    }
}

void config_adc(SFE_ADS122C04* mySensor){
  //copied from https://github.com/sparkfun/SparkFun_ADS122C04_ADC_Arduino_Library/blob/main/examples/Qwiic_PT100_ADS122C04/Example9_ManualConfig/Example9_ManualConfig.ino
  mySensor->setInputMultiplexer(ADS122C04_MUX_AIN1_AIN0); // Route AIN1 and AIN0 to AINP and AINN
  mySensor->setGain(ADS122C04_GAIN_1); // Set the gain to 1
  mySensor->enablePGA(ADS122C04_PGA_DISABLED); // Disable the Programmable Gain Amplifier
  mySensor->setDataRate(ADS122C04_DATA_RATE_20SPS); // Set the data rate (samples per second) to 20
  mySensor->setOperatingMode(ADS122C04_OP_MODE_NORMAL); // Disable turbo mode
  mySensor->setConversionMode(ADS122C04_CONVERSION_MODE_SINGLE_SHOT); // Use single shot mode
  mySensor->setVoltageReference(ADS122C04_VREF_INTERNAL); // Use the internal 2.048V reference
  mySensor->enableInternalTempSensor(ADS122C04_TEMP_SENSOR_ON); // Disable the temperature sensor
  mySensor->setDataCounter(ADS122C04_DCNT_DISABLE); // Disable the data counter (Note: the library does not currently support the data count)
  mySensor->setDataIntegrityCheck(ADS122C04_CRC_DISABLED); // Disable CRC checking (Note: the library does not currently support data integrity checking)
  mySensor->setBurnOutCurrent(ADS122C04_BURN_OUT_CURRENT_OFF); // Disable the burn-out current
  mySensor->setIDACcurrent(ADS122C04_IDAC_CURRENT_OFF); // Disable the IDAC current
  mySensor->setIDAC1mux(ADS122C04_IDAC1_DISABLED); // Disable IDAC1
  mySensor->setIDAC2mux(ADS122C04_IDAC2_DISABLED); // Disable IDAC2

  mySensor->enableDebugging(Serial); //Enable debug messages on Serial
  mySensor->printADS122C04config(); //Print the configuration
  mySensor->disableDebugging(); //Enable debug messages on Serial

  mySensor->configureADCmode(ADS122C04_RAW_MODE);

  Serial.println("Configured ADC");
}

/**
 * Unit conversion based on magic ADC numbers.
 * Don't question it.
*/
double adc_to_psi5k(uint32_t val){
  double volts = (val-2147483648)/4096000.0;
  Serial.println(volts);
  double psi = 1250 * 2 * volts - 625;
  return psi;
}

double adc_to_psi1k(uint32_t val){
  double volts = (val-2147483648)/4096000.0;
  Serial.println(volts);
  double psi = 2 * 250 * volts - 125;
  return psi;
}

double adc_to_volt(uint32_t val){
  return (val-2147483648)/4096000.0;
}

void bang_bang(){
  for(SingleSensorConfig sensor : all_sensors){
    if (sensor.pin_num == sensor_ox_pin_num){
      ox_adc_ptr = sensor.adc_ptr;  
    }
    if (sensor.pin_num == sensor_fuel_pin_num){
      fuel_adc_ptr = sensor.adc_ptr;  
    }
  }

  //Serial.println("Taking reading");
  uint32_t ox_reading;
  double ox_pressure;
  uint32_t fuel_reading;
  double fuel_pressure;

  if(do_bang_bang_ox && ox_adc_ptr) {
    ox_reading = i2c_adc_1_wire(ox_adc_ptr, sensor_ox_pin_num/10 + 64, sensor_ox_pin_num%10);
    ox_pressure = adc_to_psi5k(ox_reading);

    //set flags
    if(ox_pressure < OX_PRESS_LOWER_BOUND_PSI){
      PRESS_OX_flag = true;
    }
    if (ox_pressure > OX_PRESS_UPPER_BOUND_PSI){
      PRESS_OX_flag = false;
    }
    if (ox_pressure < OX_CLOSE_VENT_BOUND_PSI){
      VENT_OX_flag = false;
    }
    if (ox_pressure > OX_OPEN_VENT_BOUND_PSI){
      VENT_OX_flag = true;
    }
    for (int n : VENT_OX_pin_nums){
        if (USE_TANK_STAND_SERVOS)
          servo_write(PWMServo(), n, !(VENT_OX_flag ? 180 : 0));
        else
          digital_write(n, !VENT_OX_flag);
    }
    for (int n : PRESS_OX_pin_nums){
        digital_write(n, PRESS_OX_flag);
    }
  } else {
    do_bang_bang_ox = false;  
  }
  
  if(do_bang_bang_fuel && fuel_adc_ptr){
    
    fuel_reading = i2c_adc_1_wire(fuel_adc_ptr, sensor_fuel_pin_num/10 + 64, sensor_fuel_pin_num%10);
    //fuel_pressure = adc_to_psi5k(fuel_reading);
    fuel_pressure = adc_to_psi1k(fuel_reading);
    //set flags
    if(fuel_pressure < FUEL_PRESS_LOWER_BOUND_PSI){
      PRESS_FUEL_flag = true;
    }
    if (fuel_pressure > FUEL_PRESS_UPPER_BOUND_PSI){
      PRESS_FUEL_flag = false;
    }
    if (fuel_pressure < FUEL_CLOSE_VENT_BOUND_PSI){
      VENT_FUEL_flag = false;
    }
    if (fuel_pressure > FUEL_OPEN_VENT_BOUND_PSI){
      VENT_FUEL_flag = true;
    }
    for (int n : VENT_FUEL_pin_nums){
        if (USE_TANK_STAND_SERVOS)
          servo_write(PWMServo(), n, (VENT_FUEL_flag ? 180 : 0));
        else
          digital_write(n, !VENT_FUEL_flag);
    }
    for (int n : PRESS_FUEL_pin_nums){
        digital_write(n, PRESS_FUEL_flag);
    }
  } else {
    do_bang_bang_fuel = false;  
  }
}
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
void loop()
{
    // if there's data available, read a packet
    int packetSize = Udp.parsePacket();
    //Serial.println(packetSize);
    //Serial.print(" ");
    uint32_t loop_start_time = millis();
    
    if (packetSize)
    {
        #ifdef ENABLE_DEBUG
        Serial.print("Received packet of size ");
        Serial.println(packetSize);
        Serial.print("From ");
        #endif
        
        cold_fireX_time = millis() + cold_fireX_delay;
        hot_fireX_time = millis() + hot_fireX_delay;
        
        IPAddress remote = Udp.remoteIP();
        for (int i = 0; i < 4; i++)
        {
            Serial.print(remote[i], DEC);
            if (i < 3)
            {
                Serial.print(".");
            }
        }
        #ifdef ENABLE_DEBUG
        Serial.print(", port ");
        Serial.println(Udp.remotePort());
        #endif

        // read the packet into packetBufffer
        Udp.read(packetBuffer, 64);
        parsePacket(packetBuffer);
    }else{
      //Serial.println("No packet!"); 
      // Read sensors and send data (if we don't have actuator commands to run now)
      int i = 0;
      //Serial.println(all_sensors.size());
	    for(SingleSensorConfig sensor : all_sensors){
        
        //Serial.println("for loop!");

	    	if(sensor.interface_type_number == TEENSY_ADC){ // Teensy ADC
         
          //argument 0 not actually used in code. Don't know why that's there.
          int reading = teensy_analog_read(sensor.pin_num, 0);
	    		write_to_telemetry_array(telemetry_to_send,reading,i,sensor.pin_num);
	    	}
	    	else if(sensor.interface_type_number == I2C_ADC_1CH){ // i2c ADC 1 channel
          //Serial.println("1ch");
          //for an explanation of the screwed up pin numbers, see fakeMote.py
          //Serial.println(sensor.pin_num/10 + 64);
          uint32_t reading = i2c_adc_1_wire(sensor.adc_ptr, sensor.pin_num/10 + 64, sensor.pin_num%10);
	    		write_to_telemetry_array(telemetry_to_send,reading,i,sensor.pin_num);
	    	}else if(sensor.interface_type_number == I2C_ADC_2CH){
	    	  // i2c ADC 2 channel
	    		//TODO read 2 channel ADC sensor.pin_num
          uint32_t reading = i2c_adc_2_wire(sensor.adc_ptr, sensor.pin_num/10 + 64, sensor.pin_num%10, 0);
          write_to_telemetry_array(telemetry_to_send,reading,i,sensor.pin_num);         
	    	}else if(sensor.interface_type_number == FLOWMETER){ // FlowMeter
	    		//WARNING: This is legacy code and currently does nothing. Re-implement for DL.
	    		write_to_telemetry_array(telemetry_to_send,flowmeter_read_wrapper(),i,sensor.pin_num);
	    	}else if (sensor.interface_type_number >= I2C_ADC_2CH_MIN_GAIN && sensor.interface_type_number <= I2C_ADC_2CH_MAX_GAIN){
          int pga_gain_code = sensor.interface_type_number - 6;
          //Serial.print("PGA gain code: ");
          //Serial.println(pga_gain_code);
          uint32_t reading = i2c_adc_2_wire(sensor.adc_ptr, sensor.pin_num/10 + 64, sensor.pin_num%10,pga_gain_code);
          write_to_telemetry_array(telemetry_to_send,reading,i,sensor.pin_num);
        } else if (sensor.interface_type_number == INTERNAL_TEMP){
          //truncate to nearest int (*C). We can make this sensible if we need more exact temperature values
          //but the noise floor on the thermocouple is so bad this should be fine
          if (ticks % 2000 == 0){
            uint32_t pre_temp_time = millis();
            int reading = (int)(1000 * i2c_adc_internal_temp(sensor.adc_ptr, sensor.pin_num/10 + 64));
            write_to_telemetry_array(telemetry_to_send,reading,i,sensor.pin_num);
            Serial.printf("Temp time: %d ms\n", millis() - pre_temp_time);
          }
        }
        else if (sensor.interface_type_number >= SPI_ADC_1CH && sensor.interface_type_number <= SPI_ADC_2CH_MAX_GAIN) {
          AD7193_reading_t reading;
          if (sensor.pin_num / 10 == 0) {
            reading = read_AD7193(spi_adc_config_1);
          } else {
            reading = read_AD7193(spi_adc_config_2);
          }

          Serial.println(reading.result);
          Serial.println(reading.channel + (10 * (sensor.pin_num/10)));

          write_to_telemetry_array(
            telemetry_to_send,
            reading.result * 1000,
            i,
            reading.channel + (10 * (sensor.pin_num/10)));
        }
        else{
          Serial.println(sensor.interface_type_number);
		    	Serial.println("Error. Sensor Interface number is not valid");
	    	}
	    	i++;
	    }
      uint32_t bang_bang_status = do_bang_bang_ox | (do_bang_bang_fuel << 1) | (hot_fireX << 2);
      write_to_telemetry_array(telemetry_to_send,bang_bang_status,i,99); 
      //Serial.println(Udp.remoteIP());
      //Serial.printf("Loop Time (pre-UDP): %d ms\n", millis() - loop_start_time);

      if (Udp.remoteIP()){
  	    Udp.beginPacket(Udp.remoteIP(), 8888);
        Udp.write(telemetry_to_send.data(), telemetry_to_send.size());
  	    Udp.endPacket();
      }
      telemetry_to_send.clear();
      
      //do bang-bang control
      if (moteID == BANG_BANG_BOX_NUM)
        bang_bang();

      //Serial.println(millis());
      //Serial.println(cold_fireX_time);
  
      if (do_fireX && hot_fireX && millis() >= hot_fireX_time){
        Serial.println("HOT FAIL!!");
        hot_fail();
      }
      if (do_fireX && !hot_fireX && millis() >= cold_fireX_time){
        Serial.println("COLD FAIL!!");
        cold_fail();        
      }
      
      delay(loop_delay_ms);
      ticks += 1;
	}
}

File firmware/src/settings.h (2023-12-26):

#define DO_FIREX true
#define USE_TANK_STAND_SERVOS false

//#define ENABLE_DEBUG`

//IN MILLISECONDS. IF YOU SET IT IN SECONDS, MINUTES, HOURS, ETC, YOU WILL HAVE A BAD TIME!
#define COLD_FIREX_TIME_DEFAULT 30 * 60 * 1000 //30 minutes
#define HOT_FIREX_TIME_DEFAULT 120 * 1000 //120 seconds

#define FIREX_BOX_NUM '3' //must be an ASCII char, e.g. '2'

#define FIREX_PIN_NUM 35
#define FIREX_DUMP_PIN_NUM 32

#define BANG_BANG_BOX_NUM '3'

#define NO2_VENT_PIN_NUM {33}
#define IPA_VENT_PIN_NUM {30}
#define NO2_PRESS_PIN_NUM {32}
#define IPA_PRESS_PIN_NUM {23}

#define IPA_SENSOR_PIN_NUM {21}
#define NO2_SENSOR_PIN_NUM {33}

#define OX_PRESS_LOWER_BOUND_PSI 750
#define OX_PRESS_UPPER_BOUND_PSI 800
#define OX_OPEN_VENT_BOUND_PSI 1000
#define OX_CLOSE_VENT_BOUND_PSI 900

#define FUEL_PRESS_LOWER_BOUND_PSI 750
#define FUEL_PRESS_UPPER_BOUND_PSI 780
#define FUEL_OPEN_VENT_BOUND_PSI 850
#define FUEL_CLOSE_VENT_BOUND_PSI 825

#define MOTE1_INITIALLY_POWERED_SOLENOIDS {}
#define MOTE2_INITIALLY_POWERED_SOLENOIDS {34, 35}
#define MOTE3_INITIALLY_POWERED_SOLENOIDS {33}  

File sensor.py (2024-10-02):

import csv
import re
import os
import ast
import time

sensor_log_path = "logs/sensor_log_"

internal_temp = 20 # assume room temp
SCALE_INTERNAL_TEMP = False

sensor_TTL = 100 # number of polls sensor is considered alive without data (20 polls = 1 second)

sensor_offset = {} # To keep track of taring
sensor_units = {}  # Store the units corresponding to each sensor P and ID
sensor_data_TTL = {} # Keeps track of how many more polls can be without new data for a sensor before it is considered disconnected
raw_data_dict = {} # Contains raw sensor data
processed_data_dict = {} # Contains tared and unit converted data 
config_file_name = None

def initialize_sensor_info(sensor_list, config_name): 
    global config_file_name
    config_file_name = config_name
    csv_header_list = ['Timestamp (ms)']
    for sensor in sensor_list:
        sensor_offset[sensor['P and ID']] = 0
        sensor_data_TTL[sensor['P and ID']] = sensor_TTL
        sensor_units[sensor['P and ID']] = sensor["Unit"]
        csv_header_list.append(sensor["P and ID"] + "_raw")
        csv_header_list.append(sensor["P and ID"] + "_value")
        csv_header_list.append(sensor["P and ID"] + "_offset")
        raw_data_dict[sensor['P and ID']] = None
        processed_data_dict[sensor['P and ID']] = None

    sensor_offset_from_csv = {}
    try: 
        with open('./static/sensor_offset_' + config_file_name + '.csv', mode='r', newline='') as file:
            csv_reader = csv.reader(file)
            csv_dict = next(csv_reader, None)[0] # reads first row, before any comma outside double quotes
            sensor_offset_from_csv = ast.literal_eval(csv_dict) # parses string dict to a python dict, preserving data types
        for key in sensor_offset_from_csv: # update sensor_offset with offsets from the csv if they exist in sensor_offset, meaning in our current config
            if key in sensor_offset:
                sensor_offset[key] = sensor_offset_from_csv[key]
    except:
        print ("no offset file found")

    # initialize sensor_log
    global sensor_log_path
    global folder_path 
    

    if not os.path.exists("logs"): 
        print("directory for logs created! ")
        os.mkdir("logs")
    
    folder_name = time.strftime("%Y-%m-%d") + "_" + config_name 
    folder_path = os.path.join("logs",folder_name)

    if not os.path.exists(folder_path): 
        print(f"Creating {folder_name}")
        os.mkdir(folder_path)




    filenames = sorted(
        list(filter(lambda flname: re.search(r'sensors_\d+\.csv', flname), 
        next(os.walk(folder_path), (None, None, []))[2])),
        key=lambda flname: int(re.search(r'\d+', flname).group())
    )

    try:
        current_filenum = int(re.findall(r'\d+', filenames[-1])[0]) + 1 # r makes python interpret \ as a regular character instead of an escape character
    except: 
        current_filenum = 1

    sensor_filename = f"sensors_{current_filenum}.csv"
    sensor_log_path = os.path.join(folder_path, sensor_filename)
    print(sensor_log_path)
    with open(sensor_log_path, "w", newline="") as file:
        writer = csv.writer(file) 
        writer.writerow(csv_header_list)
        file.flush()
        file.close()

def file_num_from_name(fname):
    try:
        return int(re.findall(r'\d+', fname)[0]) + 1 # r makes python interpret \ as a regular character instead of an escape character
    except:
        return 0

def get_sensor_data():
    global processed_data_dict
    global raw_data_dict
    # decrease sensor TTL
    for sensor in sensor_data_TTL:
        if sensor_data_TTL[sensor] > 0 :
            sensor_data_TTL[sensor] -= 1
        else:
            processed_data_dict[sensor] = None
            raw_data_dict[sensor] = None
    return processed_data_dict

def tare(sensor_id):
    if sensor_offset[sensor_id] == 0:
        sensor_offset[sensor_id] = processed_data_dict[sensor_id]
        writeTare_Untare()

def untare(sensor_id):
    sensor_offset[sensor_id] = 0
    writeTare_Untare()

def writeTare_Untare():
    global config_file_name
    with open('./static/sensor_offset_' + config_file_name + '.csv', mode='w', newline='') as file: # clears file on open
        writer = csv.writer(file)
        writer.writerow([sensor_offset])

load_cell_filter = 0

def process_sensor_data(sensor_id, sensor_data):
    global internal_temp
    val_in_volts = sensor_data / 1e6
    processed_value = None

    match sensor_units[sensor_id]:
        case "Volts":
            processed_value = val_in_volts
        case "PSI_S1k":
            processed_value = 250 * val_in_volts - 125
        case "PSI_H5k":
            processed_value = 1250 * val_in_volts - 625
        case "PSI_M1k":
            processed_value = (1000.0 * val_in_volts)/(0.100 * 128)
        case "PSI_M5k":
            processed_value = (5000.0 * val_in_volts)/(0.100 * 128)
        case "Degrees C":
            processed_value = (195.8363374*val_in_volts + 5.4986782) + internal_temp
        case "Volts":
            processed_value = val_in_volts
        case "C Internal":
            internal_temp = sensor_data/1000 if SCALE_INTERNAL_TEMP else sensor_data
            processed_value = internal_temp
        case "lbs_tank":
            processed_value = val_in_volts*1014.54 - 32.5314
        case "lbs_engine":
            processed_value = (-val_in_volts*5128.21 - 11.2821)/2
        case "alt_ft":
            processed_value = sensor_data * 3.281 #m to ft. Dammit Kamer!
        case "alt_hpa":
            processed_value = sensor_data / 1000 # dpa to hpa
        case "alt_C":
            processed_value = sensor_data / 1000 # to degrees C
        case "g_force":
            processed_value = sensor_data * 0.00102 # cm/s^2 to G
        case "loop_ms":
            processed_value = sensor_data / 1_000
        case "Rail_Voltage":
            processed_value = val_in_volts * 23 * 1000
        case "Lora_Data":
            processed_value = sensor_data
        case "lbm_10k":
            global load_cell_filter
            processed_value = -5116.72 * val_in_volts + 59.7549
            load_cell_filter = processed_value * 0.1 + load_cell_filter * 0.9
            processed_value = load_cell_filter
        case _ :
            pass
            print("Unexpected Unit")

    return processed_value - sensor_offset[sensor_id]
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

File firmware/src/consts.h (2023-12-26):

// Network constants.
#define PORT 8888

#define MAC1 {0x36, 0x47, 0xA4, 0x6B, 0x46, 0x13}
#define MAC2 {0x28, 0x64, 0x53, 0xE8, 0xAE, 0xF8}
#define MAC3 {0x9C, 0xAA, 0x98, 0xE1, 0x26, 0x25}
#define MAC4 {0x7D, 0x99, 0x8F, 0x1B, 0xF0, 0x8A}

// Sensor constants
typedef enum {
    TEENSY_ADC = 1,
    I2C_ADC_1CH,
    I2C_ADC_2CH,
    FLOWMETER,
    I2C_ADC_2CH_MIN_GAIN = 7,
    I2C_ADC_2CH_MAX_GAIN = 13,
    INTERNAL_TEMP,
    SPI_ADC_1CH,
    SPI_ADC_2CH,
    SPI_ADC_2CH_MIN_GAIN,
    SPI_ADC_2CH_MAX_GAIN = 23,
} sensor_interface_num_t;

#define SENSOR_CLEAR_CODE 44

// Actuator constants
typedef enum {
    PWM_SERVO = 5,
    BINARY_LOAD_SWITCH,
    BANG_BANG_CONTROL = 41,
    AUTO_FIREX_CONTROL,
    HEARTBEAT
} actuator_interface_num_t;

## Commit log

2023-12-26 requirements and folder refactor
    [HighCurrentCtrl.sch, LD2_config.csv, MinOScfg.csv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]
2023-12-27 flask gui
    [example_config2.csv]
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2023-12-27 Placed buttons inside container
    - cleaned up repeated code
2023-12-27 Revert "better buttons"
    This reverts commit 9b7cf012b878d2701775844e0bdb4d0b0a95b217.
2023-12-27 update draggable buttons
    - combine on/off buttons into draggable container
    - added button name
    - updated button style
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2023-12-27 Fixed unable to submit coordinates
    file was opened as read only
    [app.py]
2023-12-27 fixed on/off buttons
    -changed buttons to div
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2023-12-27 25px offset for menu bar and button status
2023-12-27 all actuators turned off on page load, other small changes
2023-12-27 button config almost correct overlay
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2023-12-28 moved over to websocket for actuators.html page, need websocket for / and /loadconfig
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2024-01-02 renamed global variable sensors to sensor_list to avoid conflicts with html get function 'sensors' when using hardcoded dummy data
    [app.py]
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2024-01-03 sensors on p&id view page, seperate table style pages for sensors and actuators
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2024-01-03 Added graph toggle
    - checkbox for each sensor, graph appears when checked
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2024-01-06 performance tests and websocket lag fixed
    [app.py]
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2024-01-08 arm/disarm button now uses sockets instead of POST, no longer sending timestamps
    [app.py]
2024-01-08 Implemented charts that plot lines when checkbox checked
    - still needs y-axis scale
    - still needs labelled/colored lines
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2024-01-08 Fixed data duplication bug
    - if two or more charts were plotting the same sensor data updates were done multiple times
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2024-01-09 Fixed graph data alignment on x-axis
    [app.py]
2024-01-10 Added fixed testing requirements
    [app.py]
2024-01-11 config button uploads config, sig figs updated on sensors page and graphs
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2024-01-12 Prevent relaunching after cancel without reuploading file
    [app.py]
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2024-01-13 dependencies in project folder, standardization of variable names, comments
    flask and flask-socketio are added into a folder. now a computer only needs python to run this gui
2024-01-14 production server eventlet used
    [switch_arm64_masm.obj, switch_x64_masm.obj]
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2024-01-30 require gtk3
    [long_test.csv]
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2024-02-09 Created networking skeleton
    [fuel_code_flow.csv, ox_cold_flow.csv, solenoid_test_commands.csv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]
2024-02-09 Send heartbeats to MoTE
    [abort_redline.csv, m5_config.csv]
2024-02-09 autoseq actuators synced with other pages, boolean value in python prevents double clicks of launch button, pages update sensors+actuators on config upload, when disarmed sensor buttons can be clicke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
    [app.py]
2024-02-09 send actuators commands to mote on button press
    [abort.csv, abort_redline.csv, alt_redline.csv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]
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2024-02-09 removed files listed in .gitignore
    [HighCurrentCtrl.sch, LD2_config.csv, MinOScfg.csv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]
2024-02-10 autoseq changes and server change
    [switch_arm64_masm.obj, switch_x64_masm.obj]
2024-02-11 library and autoseq changes
    [cold_flow_2023_01_28_commands.csv, m5_config.csv]
2024-02-11 updated redline file
    [abort_redline.csv, m5_config.csv, testcfg.csv]
2024-02-11 tims changes
    [gse_config.csv, gse_test_seq.csv]
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2024-02-11 added sensor data example
    [actuator_log_0.csv, actuator_log_1.csv, actuator_log_10.csv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]
2024-02-12 new config and TODO
    [teensy_with_LEDS.csv]
2024-02-12 parse sensor data into frontend
    [actuator_log_0.csv, actuator_log_1.csv, actuator_log_10.csv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]
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2024-02-12 fixed mote id in sensor telemetry
    [networking.py]
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2024-02-19 Generalized autosequence functions
    [m5_config.csv]
2024-02-19 configs and lora mote
    [LoRaConfig.csv, pipeburst.csv]
2024-02-20 Implemented abort sequence
    [abort.csv, hot_fire_config.csv]
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2024-02-21 socket issues
    [gse_config.csv]
2024-02-21 lora config and networking takes signed ints now
    [LoRaConfig.csv]
2024-02-22 updated index page
    - check config file format
    - appearance update
    [hot_fire_config.csv]
2024-02-23 sample autoseq file
    [example2autoseq.csv]
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2024-02-25 added 'unit' for config file and pythonping stuff
    [teensy_with_LEDS.csv]
2024-02-26 implemented tare and untare
    [teensy_with_LEDS.csv]
2024-02-26 sessionID's and local libs might be fixed
    [app.py, networking.py, sensor.py]
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2024-02-27 Autosequence page update and fixed taring
    [gse_config.csv, hot_fire_config.csv, m5_config.csv]
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2024-02-27 reorganized files
    [HighCurrentCtrl.sch, LD2_config.csv, LoRaConfig.csv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]
2024-02-28 execute_abort_sequence now uses the same (more accurate) timing method as execute_autosequence, as opposed to delays which drift by +- 50msec
    [app.py]
2024-02-28 new ping that works on linux; all threads start on launch and handle all states; removed 'guion' socket emit from index.html as it did nothing; connect status is packet based instead of ping based
2024-02-28 Implemented redline upload
    [alt_redline.csv]
2024-02-29 implemented actuator logging (on change)
    - logging based on actuator acknowledgement, if same button is clicked multiple times it logs multiple times
    [sensor_log_27022024_124649.csv, sensor_log_27022024_124731.csv, sensor_log_27022024_125035.csv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]
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2024-03-01 Updated status bar for each page
    - added connection status
    - added system time
    - added arm/disarm button
2024-03-02 Fixed autosequence bug and added watermark
    [icarus_config.csv]
2024-03-06 Autosequence debug
    - fixed arm/disarm buttons displaying wrong state on reload
    - Prevent autosequence when disarmed & display disarmed alert
    [app.py]
2024-03-07 Config changes
    [gse_config.csv, icarus_config.csv]
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2024-03-07 Fixed sensor graph sizing bug
2024-03-08 fixed horizontal scrolling on actuators and home page
2024-03-08 Fixed overlaping pin numbers
    [networking.py]
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2024-03-12 Implemented sensor limit check
    - redline limit is considered exceeded when x consecutive number of datapoints is outside the bounds (currently x = 10)
2024-03-12 Implemented redline threshold display on sensor graphs
    - only displays when relevant sensors checked
    - only displays when datapoints close to threshold
    [teensy_test_redline.csv]
2024-03-12 Fixed sensor threshold display
    - increased range of graph to 10% above and below max and min data
    - added threshold line labels
2024-03-12 Fixed redline switch issues
    - fixed reversed colors
    - added labels in top of switches
2024-03-15 Fixed redline switch not reflecting redline state
2024-03-15 Fixed sensor tare bug
    [app.py, sensor.py]
2024-03-15 fixed sensor unit convert bug
    [configuration.py, sensor.py]
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2024-03-15 fixed sensor data timeout bugs
    [sensor.py]
2024-03-15 Improved sensor data display + logging efficiency and fixed sensor packet polling bug
    - combined sensor logging and display processing/sending of data
    [networking.py, sensor.py]
2024-03-16 Fixed sensor timeout bugs
    [sensor.py]
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2024-03-16 fixed actuator buttons on pidview, no acks yet
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2024-03-16 tims changes + update sensor page to column layout
    [gse_config.csv, icarus_config.csv]
2024-03-22 Updated tare/untare button to reflect state
    [dummy_auto.csv, icarus_config.csv, sep_rec_auto.csv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]
2024-03-22 fixed sensor table padding
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2024-03-23 Enabled changing mote names on the gui
    [moteNames.csv]
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2024-03-23 Caught heartbeat error and removed unused files
    [networking.py]
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2024-03-23 Fixed invalid autosequence upload bug and logging timestamp bug
    - logs headers said ms but timestamps were in s
    - certain invalid autosequence files caused an error which prevented the alert from appearing
    [actuator.py, app.py, networking.py]
2024-03-24 Fixed sensor page bugs
    - fixed offset dictionary displayed
    - fixed sensor table not scrolling
2024-03-25 Fixed actuator log naming bug
    [actuator.py, sensor.py]
2024-03-26 Fixed sensor taring bug
    [sensor.py]
2024-03-26 Fixed actuators click when mote disconnected bug
    [app.py]
2024-03-26 Fixed castrated logo on sensors page
2024-03-26 Fixed sensor graphs resetting when adding new chart
2024-04-05 implemented act buttons init to On when unpowered state set to Open
2024-04-13 bunch of little changes + optimizations
    [LoRaConfig.csv, icarus_config_bmp.csv, icarus_config_bmp_imu.csv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]
2024-04-19 Updated sensor_offset files to include config file name
    [sensor_offset.csv]
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2024-04-19 Added fakeMote + moved config files
    [gse_config.csv, icarus_config.csv, icarus_config_bmp.csv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]
2024-10-02 Updated autoseq to remain on prev frame after uploading + added logs folder sorting
    [gse_config.csv, icarus_config.csv, icarus_config_bmp.csv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]
